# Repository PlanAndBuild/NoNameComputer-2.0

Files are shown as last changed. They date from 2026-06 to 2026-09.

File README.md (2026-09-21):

<div align="center">
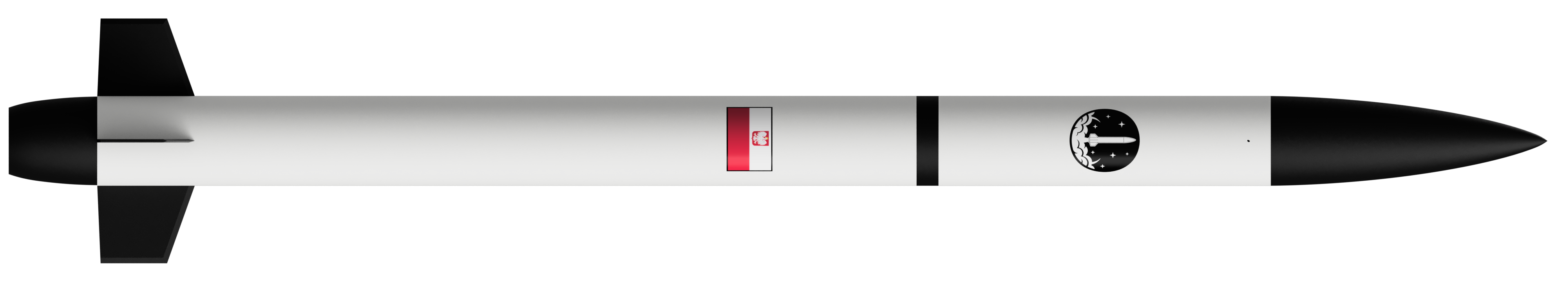
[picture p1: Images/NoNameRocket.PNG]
Render projektu
  
</div>

---

<h1 align="center">NNCpro</h1>

<h3 align="center">AKA NoNameComputer 2.0</h3>

<p align="center">
 <small><I>Built for sky.<I></small>
</p>

<p align="center">
  <b>NNCpro is a fligth computer designed mainly for rockets but it also can be used for other vehicles.</b>
  <br>
  <b>It is designed to collect data from all of the sensor, sending it IRL back down to the earth via radio link, deploy parachutes, steer rocket in flight using aerodynamic control or TVC and at the end send live location. </b>
  </br>
  <em>We have designed it for our rockets because there is no comercial computers or if there is something it's very expensive. We actually like designig electronics and thats why we're even here.</em>
</p>

## Features

**8x Servo outputs** ***(PWM channels)***

**6x Pyrotechniacal channels** ***(used for firing parachute charges, motor ignitions etc.)***

**Long-Range radio** ***(based on two LoRa modules for simultaneous transmiting and reciveing)***

**Current and Voltage sensing** ***(based on INA3221 three channel current sensor)***

**Audio signaling** ***(using passive buzzer with possibility of modulation sound wave)***

**Flash memory for storing software and flight data in flight**

**micro-SD card slot for saving fligth data after landing**

**3,3v and 5v power supply**

**ARGB LEDs for signaling computer states**

---
## Sensors
| Sensor Type | Primary Component |
| :--- | :--- |
| **Barometer main** | `MS5611` (High precision) |
| **Barometer secondary** |`BMP390` (Redundant) |
| **Inertail Mesurment Unit main**| `LSM6DSV80XTR` (6-DoF Main) |
| **Inertail Mesurment Unit secondary** |`LSM6DSO32XTR` (6-DoF Secondary) |
| **High-G Acceleration** | `H3LIS200DLTR` (Up to $\pm200\text{g}$) |
| **Magnetometer** | `MMC5983MA` (3-axis Compass) |
| **GNSS (GPS)** | `u-blox MAX-M10M-20b` |
---
## Images

<table align="center" border="0" cellpadding="0" cellspacing="0">
  <tr>
    <td>
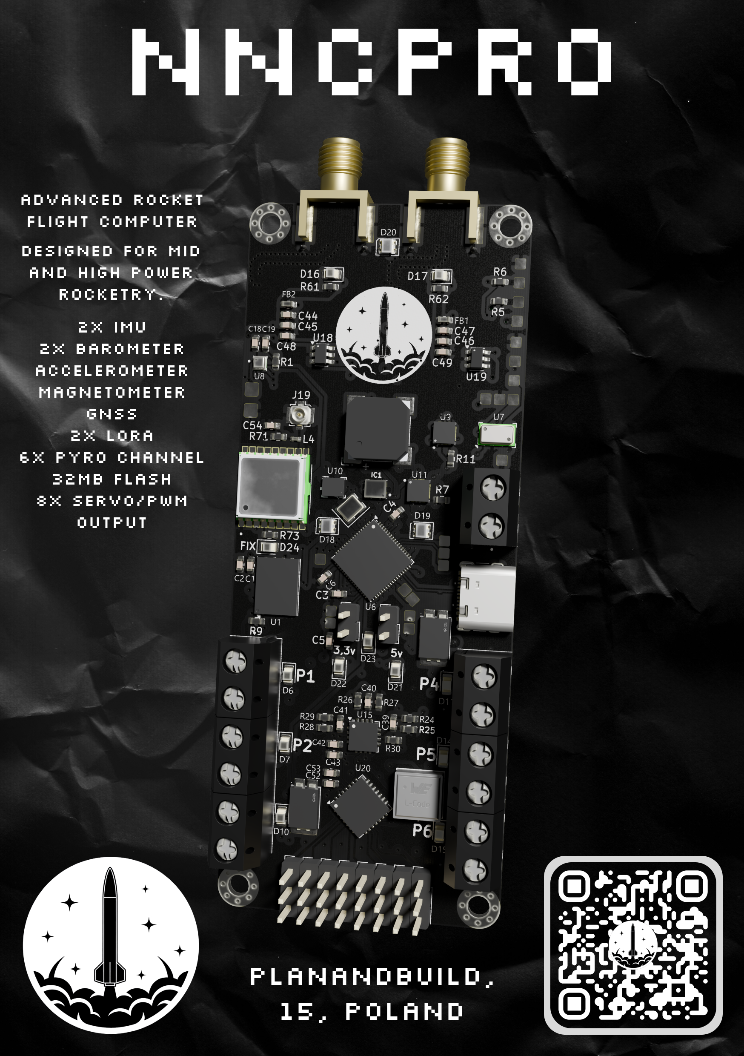
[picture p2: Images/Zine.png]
NNCpro Zine
      
    </td>
    <td>
      NNCpro Render
    </td>
  </tr>
</table>

### schematics:

 <div align="center">
  
  
  
  
  
  
</div>
 
## ⚖️ License

This project is licensed under the **Creative Commons Attribution-NonCommercial-ShareAlike 4.0 International (CC BY-NC-SA 4.0)** License.

[][cc-by-nc-sa]

You are free to share and adapt this material under the following terms:
* **Attribution** — You must give appropriate credit to the original author.
* **NonCommercial** — You may not use the material for commercial purposes.
* **ShareAlike** — If you remix, transform, or build upon the material, you must distribute your contributions under the same license.

## BOM
| Item No. | Qty | Value | Manufacturer Part Number (MPN) | Supplier Part Number | Unit Price | Total Price |
| :---: | :---: | :--- | :--- | :--- | :---: | :---: |
| | **--- CAPACITORS ---** | | | | | |
| 1 | 1 | 10nF | 0603X7R103K250NT | [C49326603](https://www.lcsc.com/product-detail/C49326603.html) | $0.0034 | $0.0034 |
| 2 | 33 | 100nF | FCC0603B104K500CT | [C5137636](https://www.lcsc.com/product-detail/C5137636.html) | $0.0147 | $0.4851 |
| 3 | 5 | 1uF | CL10B105KA8NNNC | [C29936](https://www.lcsc.com/product-detail/C29936.html) | $0.0218 | $0.1090 |
| 4 | 2 | 2.2uF | CL10A225KO8NNNC | [C23630](https://www.lcsc.com/product-detail/C23630.html) | $0.0093 | $0.0186 |
| 5 | 1 | 4.7uF | CL10A475KO8NNNC | [C19666](https://www.lcsc.com/product-detail/C19666.html) | $0.0227 | $0.0227 |
| 6 | 5 | 10uF | CL10A106MA8NRNC | [C96446](https://www.lcsc.com/product-detail/C96446.html) | $0.0532 | $0.2660 |
| 7 | 5 | 22uF | CL10A226MP8NUNE | [C86295](https://www.lcsc.com/product-detail/C86295.html) | $0.0380 | $0.1900 |
| 8 | 4 | 47uF | CL21A476MRYNNNE | [C377776](https://www.lcsc.com/product-detail/C377776.html) | $0.0542 | $0.2168 |
| | **--- RESISTORS ---** | | | | | |
| 9 | 3 | 0.03Ω | YLRY06-1-30F | [C20608713](https://www.lcsc.com/product-detail/C20608713.html) | $0.0390 | $0.1170 |
| 10 | 13 | 10Ω | 1RC0603J0100 | [C54531635](https://www.lcsc.com/product-detail/C54531635.html) | $0.0012 | $0.0156 |
| 11 | 7 | 220Ω | HRC0603F2200ENTN | [C54920883](https://www.lcsc.com/product-detail/C54920883.html) | $0.0011 | $0.0077 |
| 12 | 1 | 560Ω | GR0603J560RT5G00 | [C49653272](https://www.lcsc.com/product-detail/C49653272.html) | $0.0008 | $0.0008 |
| 13 | 1 | 1kΩ | FRC0603F1001TS | [C2907002](https://www.lcsc.com/product-detail/C2907002.html) | $0.0023 | $0.0023 |
| 14 | 2 | 4.7kΩ | HRC0603J472 ENTN | [C54921051](https://www.lcsc.com/product-detail/C54921051.html) | $0.0010 | $0.0020 |
| 15 | 2 | 5.1kΩ | RTT035101FTP | [C103686](https://www.lcsc.com/product-detail/C103686.html) | $0.0012 | $0.0024 |
| 16 | 30 | 10kΩ | FRC0603F1002TS | [C2906982](https://www.lcsc.com/product-detail/C2906982.html) | $0.0023 | $0.0690 |
| 17 | 2 | 15kΩ | SCR0603J15K | [C3017711](https://www.lcsc.com/product-detail/C3017711.html) | $0.0009 | $0.0018 |
| 18 | 1 | 30kΩ | CL0603JN30KP | [C49254202](https://www.lcsc.com/product-detail/C49254202.html) | $0.0011 | $0.0110 |
| 19 | 1 | 42.2kΩ | RS-03K4222FT | [C321903](https://www.lcsc.com/product-detail/C321903.html) | $0.0006 | $0.0006 |
| 20 | 10 | 100kΩ | CL0603JN100KP | [C46635231](https://www.lcsc.com/product-detail/C46635231.html) | $0.0011 | $0.0110 |
| 21 | 1 | 110kΩ | CL0603FN110KP | [C48996812](https://www.lcsc.com/product-detail/C48996812.html) | $0.0012 | $0.0012 |
| 22 | 1 | 135kΩ | RT0603BRD07135KL | [C861113](https://www.lcsc.com/product-detail/C861113.html) | $0.0284 | $0.0284 |
| 23 | 1 | 330kΩ | GR0603J330KT5G00 | [C49656714](https://www.lcsc.com/product-detail/C49656714.html) | $0.0008 | $0.0008 |
| | **--- INDUCTORS / CHOKES ---** | | | | | |
| 24 | 2 | 27nH | LQG15HS27NJ02D | [C12669](https://www.lcsc.com/product-detail/C12669.html) | $0.0282 | $0.0564 |
| 25 | 1 | 680nH | 7443934450068 | [710-7443934450068](https://www.mouser.pl/ProductDetail/Wurth-Elektronik/7443934450068) | $1.8700 | $1.8700 |
| 26 | 1 | 1.5uH | AFE201612S1R5MBT | [C41347749](https://www.lcsc.com/product-detail/C41347749.html) | $0.0389 | $0.0389 |
| | **--- DIODES / TRANSISTORS ---** | | | | | |
| 27 | 6 | ZMM3V0-TD | ZMM3V0-TD | [C46550821](https://www.lcsc.com/product-detail/C46550821.html) | $0.0064 | $0.0384 |
| 28 | 7 | DO2300B | DO2300B | [C41367404](https://www.lcsc.com/product-detail/C41367404.html) | $0.0190 | $0.1330 |
| 29 | 12 | LED RED | GL0805UR01 | [C51933307](https://www.lcsc.com/product-detail/C51933307.html) | $0.0046 | $0.0552 |
| 30 | 1 | SI1016CX-T1-GE3 | SI1016CX-T1-GE3 | [C727293](https://www.lcsc.com/product-detail/C727293.html) | $0.9442 | $0.9442 |
| 31 | 3 | SP15100L | SP15100L | [C20199370](https://www.lcsc.com/product-detail/C20199370.html) | $0.1170 | $0.3510 |
| 32 | 3 | WS2812B-2020 | XL-0807RGBC-2812B-S | [C41413181](https://www.lcsc.com/product-detail/C41413181.html) | $0.0345 | $0.1035 |
| | **--- INTEGRATED CIRCUITS (ICs) ---** | | | | | |
| 33 | 2 | 74LVC2G04LT06ARCQ | 74LVC2G04LT06ARCQ | [C46527078](https://www.lcsc.com/product-detail/C46527078.html) | $0.0404 | $0.0808 |
| 34 | 1 | BMP390L | BMP390L | [828-BMP390TR-ND](https://www.digikey.pl/en/products/detail/bosch-sensortec/BMP390/16164575) | $3.3000 | $3.3000 |
| 35 | 2 | E220-400M22S | E220-400M22S | [C2971737](https://www.lcsc.com/product-detail/C2971737.html) | $2.7215 | $5.4430 |
| 36 | 1 | H3LIS200DLTR | H3LIS200DLTR | [497-15698-2-ND](https://www.digikey.pl/en/products/detail/stmicroelectronics/H3LIS200DLTR/5268010) | $8.4000 | $8.4000 |
| 37 | 1 | INA3221 | INA3221AIRGVR | [C181255](https://www.lcsc.com/product-detail/C181255.html) | $1.4247 | $1.4247 |
| 38 | 1 | LSM6DSO32 | LSM6DSO32 | [497-LSM6DSO32XTR-ND](https://www.digikey.pl/en/products/detail/stmicroelectronics/LSM6DSO32XTR/14291421) | $4.8900 | $4.8900 |
| 39 | 1 | LSM6DSV80XTR | LSM6DSV80XTR | [497-LSM6DSV80XTR-ND](https://www.digikey.pl/en/products/detail/stmicroelectronics/LSM6DSV80XTR/26371340) | $6.5100 | $6.5100 |
| 40 | 1 | LT6000CDCB#TRMPBF | LT6000CDCB#TRMPBF | [C672644](https://www.lcsc.com/product-detail/C672644.html) | $3.3445 | $3.3445 |
| 41 | 1 | MAX-M10M-20B | MAX-M10M-20B | [672-MAX-M10M-20BTR-ND](https://www.digikey.pl/en/products/detail/u-blox/MAX-M10M-20B/28314774) | $7.5600 | $7.5600 |
| 42 | 1 | MMC5983MA | MMC5983MA | [C404329](https://www.lcsc.com/product-detail/C404329.html) | $2.2672 | $2.2672 |
| 43 | 1 | MS5611 | MS5611-01BA | [C15639](https://www.lcsc.com/product-detail/C15639.html) | $7.1145 | $7.1145 |
| 44 | 1 | NC7WZ07P6X | NC7WZ07P6X | [C95342](https://www.lcsc.com/product-detail/C95342.html) | $0.0564 | $0.0564 |
| 45 | 1 | PCA9685BS | PCA9685BS | [C5191634](https://www.lcsc.com/product-detail/C5191634.html) | $4.4014 | $4.4014 |
| 46 | 1 | STM32H562RIVx | STM32H562RIV6 | [497-STM32H562RIV6-ND](https://www.digikey.pl/en/products/detail/stmicroelectronics/STM32H562RIV6/21348982) | $7.3400 | $7.3400 |
| 47 | 1 | TPS564242DRLR | TPS564242DRLR | [296-TPS564242DRLRTR-ND](https://www.digikey.pl/en/products/detail/texas-instruments/TPS564242DRLR/16585669) | $0.5800 | $0.5800 |
| 48 | 1 | TPS56C230RJER | TPS56C230RJER | [C1849534](https://www.lcsc.com/product-detail/C1849534.html) | $0.5300 | $0.5300 |
| 49 | 1 | W25Q512JVE | W25Q512JVEIQ | [C2986165](https://www.lcsc.com/product-detail/C2986165.html) | $6.7941 | $6.7941 |
| | **--- CONNECTORS ---** | | | | | |
| 50 | 2 | Conn_01x02_Pin | 2.54mm Header 2pin | [Numer](Link) | | |
| 51 | 8 | Conn_01x03_Pin | 2.54mm Header 3pin | [Numer](Link) | | |
| 52 | 2 | SMA_Connector | HL-SMA-KHDC5T | [C19712117](https://www.lcsc.com/product-detail/C19712117.html) | $2.9083 | $5.8166 |
| 53 | 1 | U.fl_Connetor | 5001-RF00001-03R1-00 | [C48689029](https://www.lcsc.com/product-detail/C48689029.html) | $0.0338 | $0.0338 |
| 54 | 1 | MLD-TF PUSH-H18 | MLD-TF PUSH-H18 | [C52750848](https://www.lcsc.com/product-detail/C52750848.html) | $0.0421 | $0.0421 |
| 55 | 7 | Screw_Terminal_01x02 | KF301-2P | [C474881](https://www.lcsc.com/product-detail/C474881.html) | $0.1008 | $0.7056 |
| 56 | 1 | USB_C_Receptacle_USB2.0_16P | F32258MUBCE2O | [C5917305](https://www.lcsc.com/product-detail/C5917305.html) | $0.3052 | $0.3052 |
| | **--- MISCELLANEOUS ---** | | | | | |
| 57 | 6 | 500mA | CF06V5TR50 | [C163116](https://www.lcsc.com/product-detail/C163116.html) | $0.0386 | $0.2316 |
| 58 | 3 | 600ohm | CBG160808U601T | [C73326](https://www.lcsc.com/product-detail/C73326.html) | $0.0113 | $0.0678 |
| 59 | 1 | Buzzer | YX-SMD8530P | [C781886](https://www.lcsc.com/product-detail/C781886.html) | $0.3755 | $0.3755 |
| 60 | 1 | Crystal_GND24 | F32258MUBCE2O | [C5917305](https://www.lcsc.com/product-detail/C5917305.html) | $0.3052 | $0.3052 |
| | **--- ADDITIONAL ELEMENTS ---** | | | | | |
| 61 | 4 | Screws | Any M3 screw |  |  |  |
| 62 | 1 | PCB Board | 4layer PCB | - | $7.0000 | $7.0000 |
| | | | | | | |
| **SUMMARY** | | | | | | **Total: $90.28** |

[cc-by-nc-sa]: http://creativecommons.org/licenses/by-nc-sa/4.0/
[cc-by-nc-sa-shield]: https://img.shields.io/badge/License-CC%20BY--NC--SA%204.0-lightgrey.svg

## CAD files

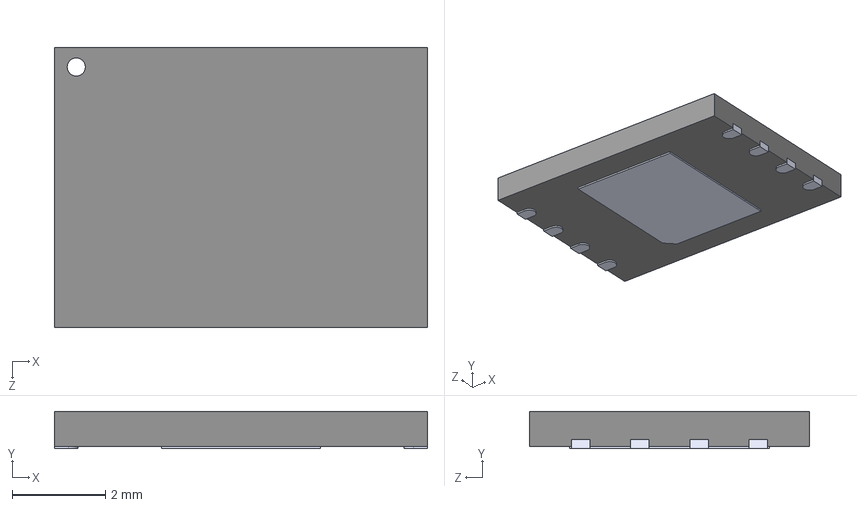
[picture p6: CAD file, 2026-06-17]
Board/3DModels/W25Q256JVEIQ TR--3DModel-STEP-269445.STEP
8.00 x 0.8 x 6.00 mm

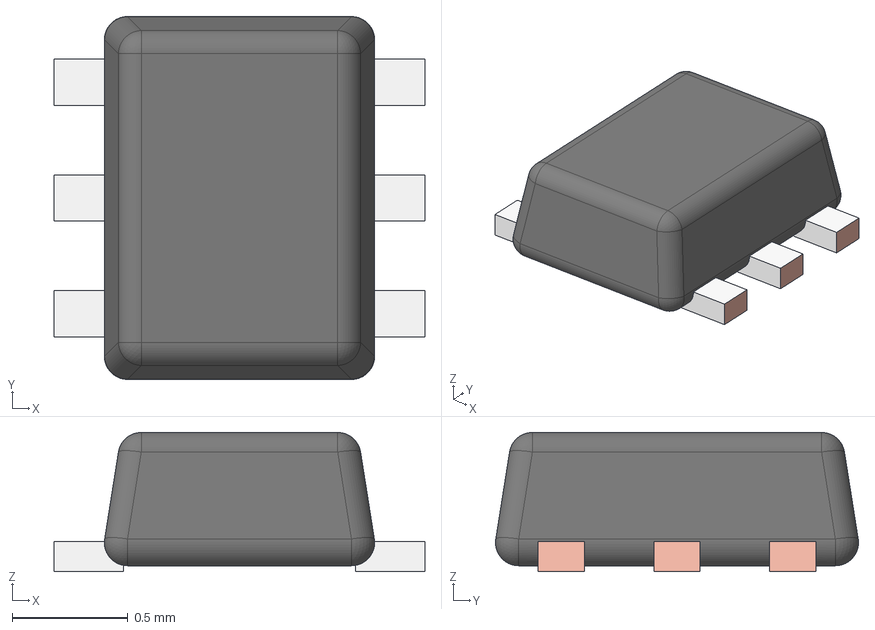
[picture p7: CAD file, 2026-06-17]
Board/3DModels/DRL0006A.stp
1.60 x 1.57 x 0.6 mm
FRAME-DRL0006A
BODY-SOT
PIN1-ID

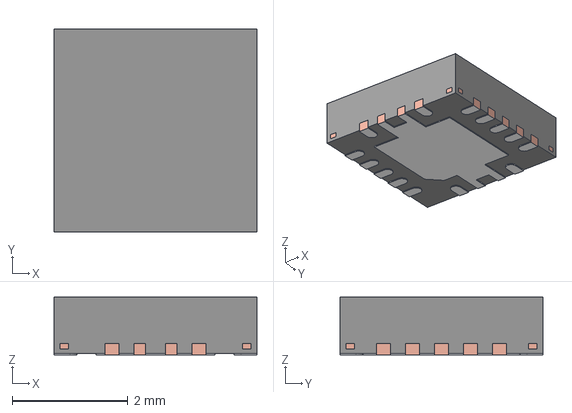
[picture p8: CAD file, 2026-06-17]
Board/3DModels/RHL0014A.stp
3.50 x 3.50 x 1.00 mm
FRAME

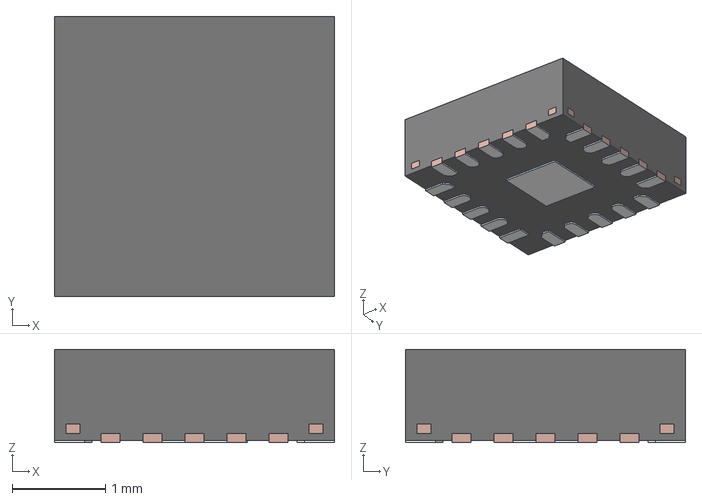
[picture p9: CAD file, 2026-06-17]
Board/3DModels/TPS56C230RJER.stp
3.00 x 3.00 x 1.00 mm
FRAME

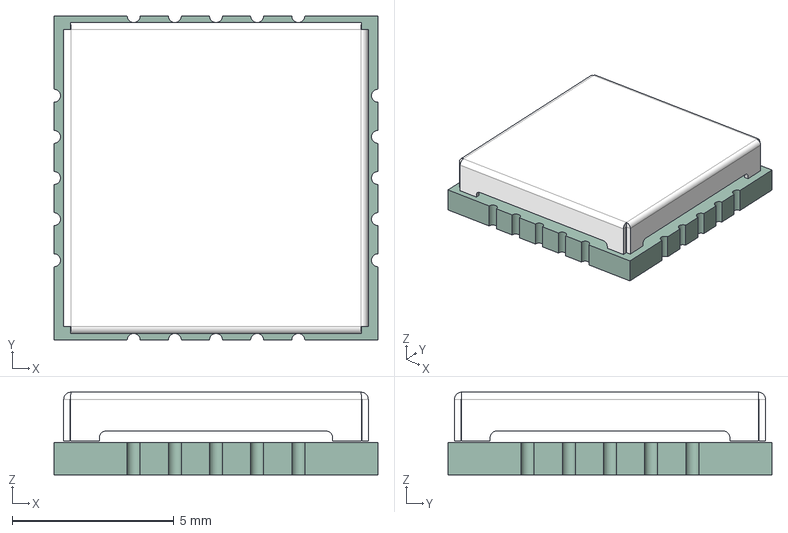
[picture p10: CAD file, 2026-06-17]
Board/3DModels/E220-400MM22S.step
10.0 x 10.0 x 2.55 mm
PBZ-135
10705-V1.1_PCB

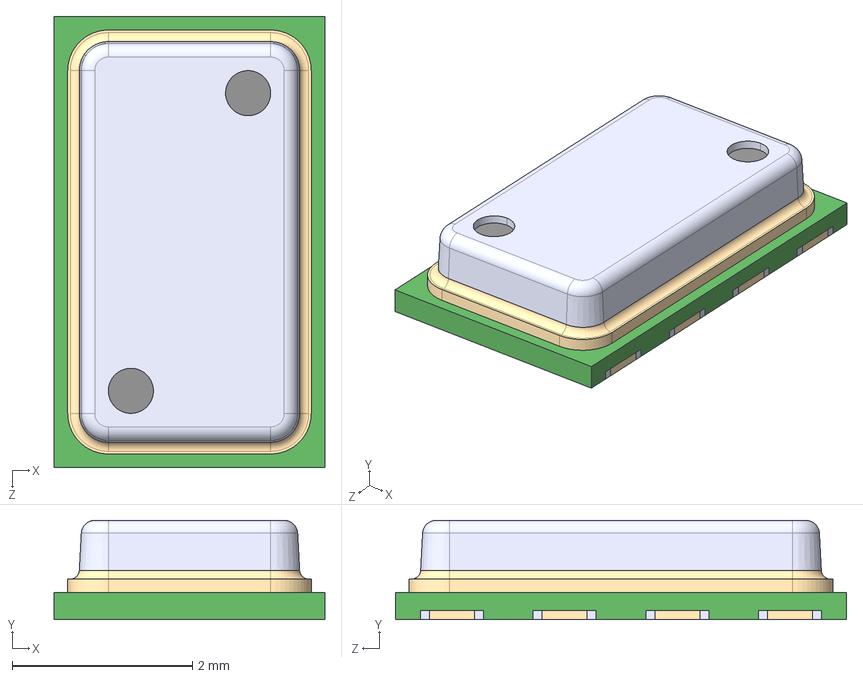
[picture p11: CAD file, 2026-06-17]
Board/3DModels/MS5611-01BA03--3DModel-STEP-510211.STEP
3.00 x 1.10 x 5.00 mm

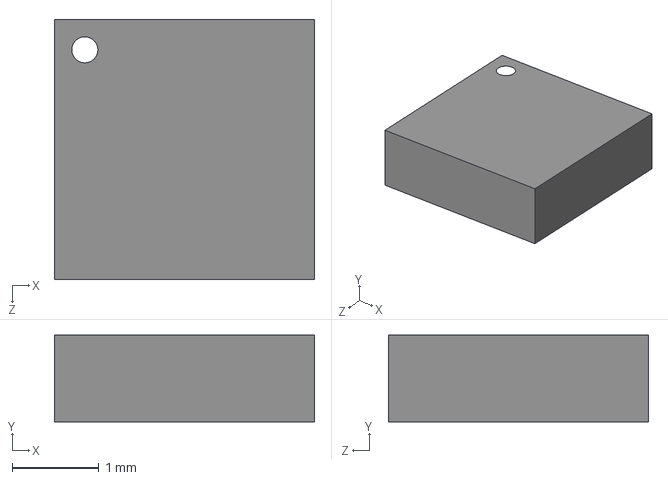
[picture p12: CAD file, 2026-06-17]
Board/3DModels/MMC5983MA.step
3.00 x 1.00 x 3.00 mm

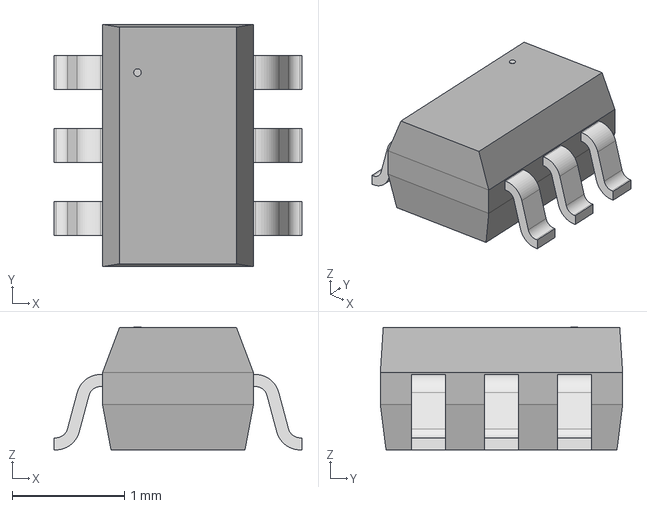
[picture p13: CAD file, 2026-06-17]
Board/3DModels/SC-70-6_PSM.step
2.21 x 2.16 x 1.09 mm

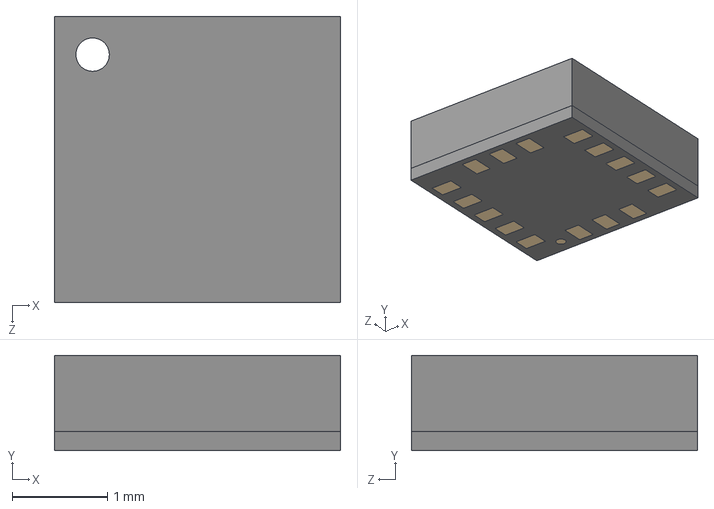
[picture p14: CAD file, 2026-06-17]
Board/3DModels/H3LIS200DLTR.step
3.00 x 1.00 x 3.00 mm

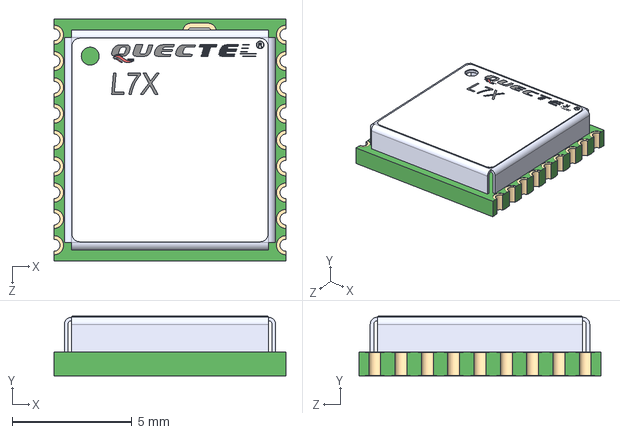
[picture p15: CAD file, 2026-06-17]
Board/3DModels/L76-L.step
9.70 x 2.49 x 10.1 mm

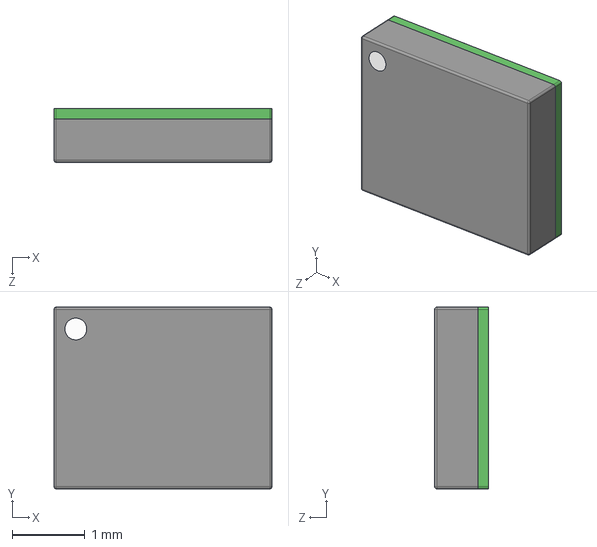
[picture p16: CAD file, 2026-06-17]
Board/3DModels/LSM6DSV80XTR.stp
3.00 x 2.50 x 0.74 mm

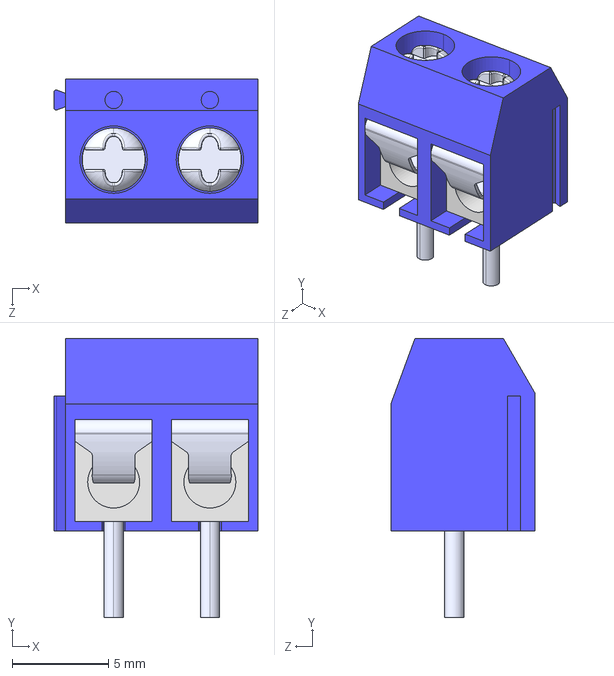
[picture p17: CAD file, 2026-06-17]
Board/3DModels/KF301-2P.step
10.6 x 14.5 x 7.50 mm

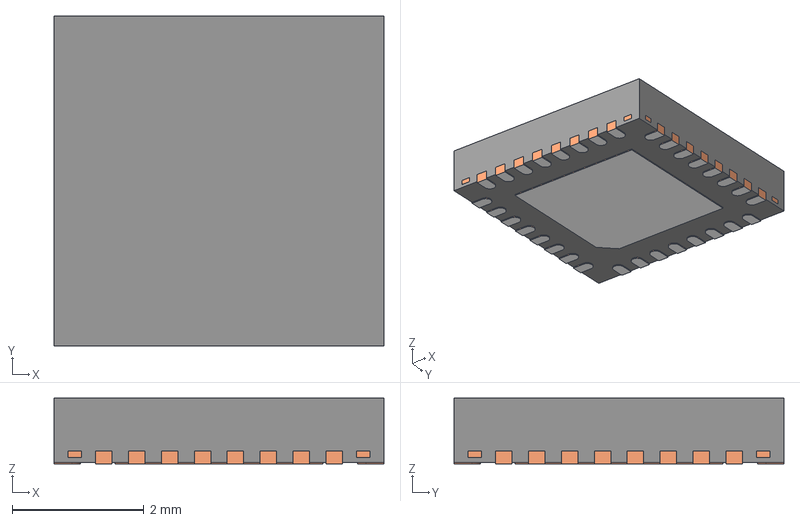
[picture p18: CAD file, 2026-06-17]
Board/3DModels/TLC5940RHBR.stp
5.00 x 5.00 x 1.00 mm
BODY-QFN
FRAME-RHB0032D
PIN1-ID

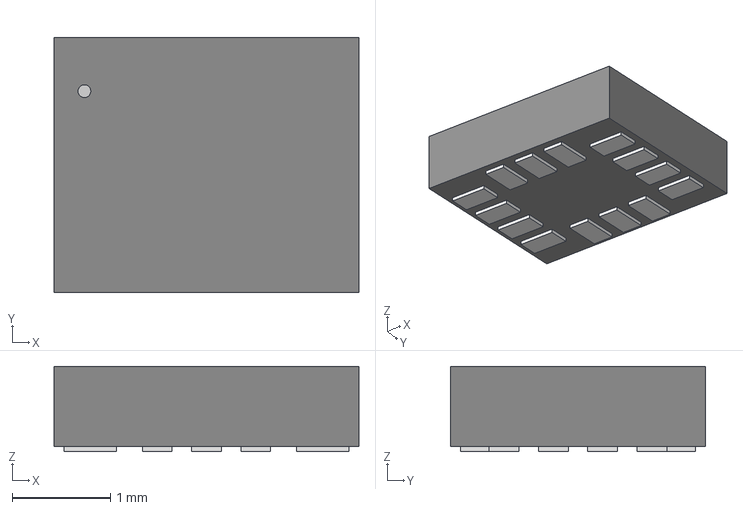
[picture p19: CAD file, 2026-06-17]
Board/3DModels/LGA-14L_2P5X3X0P83_STM.step
3.10 x 2.59 x 0.866 mm

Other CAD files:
Board/3DModels/W25Q256JVEIQ_TR.step
Board/3DModels/BMP390L.step
Board/3DModels/WS2812B2020--3DModel-STEP-269445.STEP

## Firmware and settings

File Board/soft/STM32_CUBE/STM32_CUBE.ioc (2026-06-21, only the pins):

Mcu.UserName=STM32H562RIVx
PA0.Signal=UART4_TX
PA1.GPIO_Label=GPS_RST
PA1.Signal=GPIO_Output
PA10.GPIO_Label=CS_MAG
PA10.Signal=GPIO_Output
PA11.Signal=USB_DM
PA12.Signal=USB_DP
PA13(JTMS/SWDIO).GPIO_Label=CS_H3L
PA13(JTMS/SWDIO).Signal=GPIO_Output
PA14(JTCK/SWCLK).GPIO_Label=CS_LSM1
PA14(JTCK/SWCLK).Signal=GPIO_Output
PA15(JTDI).GPIO_Label=BUSY_2
PA15(JTDI).Signal=GPIO_Input
PA3.Signal=OCTOSPI1_CLK
PA4.GPIO_Label=EN_5V
PA4.Signal=GPIO_Output
PA5.GPIO_Label=LED_1
PA5.Signal=GPIO_Output
PA6.Signal=OCTOSPI1_IO3
PA7.GPIO_Label=PYRO_1
PA7.Signal=GPIO_Output
PA9.GPIO_Label=CS_MS5611
PA9.Signal=GPIO_Output
PB0.Signal=OCTOSPI1_IO1
PB1.GPIO_Label=P_DET_2
PB1.Signal=GPIO_Input
PB10.Signal=I2C2_SCL
PB11.Signal=I2C2_SDA
PB12.GPIO_Label=P_DET_3
PB12.Signal=GPIO_Input
PB13.GPIO_Label=P_DET_6
PB13.Signal=GPIO_Input
PB14.GPIO_Label=PYRO_6
PB14.Signal=GPIO_Output
PB15.GPIO_Label=P_DET_5
PB15.Signal=GPIO_Input
PB2.GPIO_Label=PYRO_3
PB2.Signal=GPIO_Output
PB6.Signal=OCTOSPI1_NCS
PB7.GPIO_Label=CS_LoRa2
PB7.Signal=GPIO_Output
PB8.Signal=UART4_RX
PB9.GPIO_Label=DIO1_2
PB9.Signal=GPIO_Output
PC0.GPIO_Label=SepDet1
PC0.Signal=GPIO_Input
PC1.GPIO_Label=SepDet2
PC1.Signal=GPIO_Input
PC10.Signal=SPI3_SCK
PC11.Signal=SPI3_MISO
PC12.Signal=SPI3_MOSI
PC13.GPIO_Label=CS_LoRa1
PC13.Signal=GPIO_Output
PC14-OSC32_IN(OSC32_IN).GPIO_Label=DIO1_1
PC14-OSC32_IN(OSC32_IN).Signal=GPIO_Output
PC15-OSC32_OUT(OSC32_OUT).GPIO_Label=CS_BMP390
PC15-OSC32_OUT(OSC32_OUT).Signal=GPIO_Output
PC2.Signal=OCTOSPI1_IO2
PC3.Signal=OCTOSPI1_IO0
PC4.GPIO_Label=P_DET_1
PC4.Signal=GPIO_Input
PC5.GPIO_Label=PYRO_2
PC5.Signal=GPIO_Output
PC6.GPIO_Label=PYRO_4
PC6.Signal=GPIO_Output
PC7.GPIO_Label=CS_SD
PC7.Signal=GPIO_Output
PC8.GPIO_Label=CS_LSM2
PC8.Signal=GPIO_Output
PD11.GPIO_Label=PYRO_5
PD11.Signal=GPIO_Output
PD12.GPIO_Label=P_DET_4
PD12.Signal=GPIO_Input
PE0.GPIO_Label=BUSY_1
PE0.Signal=GPIO_Input
PH0-OSC_IN(PH0).Signal=RCC_OSC_IN
PH1-OSC_OUT(PH1).Signal=RCC_OSC_OUT

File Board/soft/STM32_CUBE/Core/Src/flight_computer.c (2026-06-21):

#include "flight_computer.h"
#include "sensor_ms5611.h"
#include "sensor_bmp390.h"
#include "sensor_lsm6dsv.h"
#include "sensor_lsm6dso.h"
#include "sensor_h3lis200.h"
#include "sensor_mmc5983.h"
#include "sensor_ina3221.h"
#include "gps_parser.h"
#include "lora_llcc68.h"
#include "flash_w25q.h"
#include "sd_card.h"
#include "pca9685.h"
#include "spi_common.h"
#include <stdio.h>
#include <string.h>

// Shared handles and states
extern UART_HandleTypeDef huart4;

static FlightState_t current_state = STATE_IDLE;
static float ground_altitude = 0.0f;
static uint32_t flight_start_time = 0;
static uint32_t flash_write_address = 0;
static uint32_t log_count = 0;

// Device handles
static MS5611_t ms5611;
static BMP390_t bmp390;
static LSM6DSV_t imu_main;
static LSM6DSO_t imu_sub;
static H3LIS200_t high_g;
static MMC5983_t mag;
static INA3221_t power_mon;
static GPS_Data_t *gps_ptr;

static LoRa_t lora_tx;
static LoRa_t lora_rx;

// 2-State Kalman Filter state: x = [alt, vel]^T
static float x_alt = 0.0f;
static float x_vel = 0.0f;
static float P_00 = 10.0f;
static float P_01 = 0.0f;
static float P_10 = 0.0f;
static float P_11 = 10.0f;

// Filter variances (tuning parameters)
static const float Q_alt = 0.1f;
static const float Q_vel = 0.5f;
static const float R_baro = 1.2f;

static void Kalman_Predict(float accel, float dt)
{
  // State extrapolation: x_k = F * x_{k-1} + B * u
  x_alt = x_alt + x_vel * dt + 0.5f * accel * dt * dt;
  x_vel = x_vel + accel * dt;

  // Covariance extrapolation: P = F * P * F^T + Q
  float P00_new = P_00 + dt * (P_10 + P_01 + dt * P_11) + Q_alt;
  float P01_new = P_01 + dt * P_11 + Q_alt;
  float P10_new = P_10 + dt * P_11 + Q_alt;
  float P11_new = P_11 + Q_vel;

  P_00 = P00_new;
  P_01 = P01_new;
  P_10 = P10_new;
  P_11 = P11_new;
}

static void Kalman_Update(float meas_alt)
{
  // Kalman Gain: K = P * H^T * (H * P * H^T + R)^-1
  float S = P_00 + R_baro;
  float K_0 = P_00 / S;
  float K_1 = P_10 / S;

  // State update: x = x + K * (z - H * x)
  float err = meas_alt - x_alt;
  x_alt = x_alt + K_0 * err;
  x_vel = x_vel + K_1 * err;

  // Covariance update: P = (I - K * H) * P
  float P_00_new = (1.0f - K_0) * P_00;
  float P_01_new = (1.0f - K_0) * P_01;
  float P_10_new = -K_1 * P_00 + P_10;
  float P_11_new = -K_1 * P_01 + P_11;

  P_00 = P_00_new;
  P_01 = P_01_new;
  P_10 = P_10_new;
  P_11 = P_11_new;
}

// Continuity checking helper
static uint8_t CheckPyroContinuity(uint8_t channel)
{
  GPIO_PinState state = GPIO_PIN_RESET;
  switch (channel)
  {
    case 1: state = HAL_GPIO_ReadPin(P_DET_1_GPIO_Port, P_DET_1_Pin); break;
    case 2: state = HAL_GPIO_ReadPin(P_DET_2_GPIO_Port, P_DET_2_Pin); break;
    case 3: state = HAL_GPIO_ReadPin(P_DET_3_GPIO_Port, P_DET_3_Pin); break;
    case 4: state = HAL_GPIO_ReadPin(P_DET_4_GPIO_Port, P_DET_4_Pin); break;
    case 5: state = HAL_GPIO_ReadPin(P_DET_5_GPIO_Port, P_DET_5_Pin); break;
    case 6: state = HAL_GPIO_ReadPin(P_DET_6_GPIO_Port, P_DET_6_Pin); break;
    default: break;
  }
  // Low logic level usually indicates igniter is connected (closing shunt to GND), 
  // High level means open circuit. Depending on schematic, let's return 1 for connected, 0 for open.
  return (state == GPIO_PIN_RESET) ? 1 : 0;
}

static void FirePyro(uint8_t channel)
{
  switch (channel)
  {
    case 1:
      HAL_GPIO_WritePin(PYRO_1_GPIO_Port, PYRO_1_Pin, GPIO_PIN_SET);
      HAL_Delay(1000); // 1-second pulse
      HAL_GPIO_WritePin(PYRO_1_GPIO_Port, PYRO_1_Pin, GPIO_PIN_RESET);
      break;
    case 2:
      HAL_GPIO_WritePin(PYRO_2_GPIO_Port, PYRO_2_Pin, GPIO_PIN_SET);
      HAL_Delay(1000);
      HAL_GPIO_WritePin(PYRO_2_GPIO_Port, PYRO_2_Pin, GPIO_PIN_RESET);
      break;
    case 3:
      HAL_GPIO_WritePin(PYRO_3_GPIO_Port, PYRO_3_Pin, GPIO_PIN_SET);
      HAL_Delay(1000);
      HAL_GPIO_WritePin(PYRO_3_GPIO_Port, PYRO_3_Pin, GPIO_PIN_RESET);
      break;
    case 4:
      HAL_GPIO_WritePin(PYRO_4_GPIO_Port, PYRO_4_Pin, GPIO_PIN_SET);
      HAL_Delay(1000);
      HAL_GPIO_WritePin(PYRO_4_GPIO_Port, PYRO_4_Pin, GPIO_PIN_RESET);
      break;
    case 5:
      HAL_GPIO_WritePin(PYRO_5_GPIO_Port, PYRO_5_Pin, GPIO_PIN_SET);
      HAL_Delay(1000);
      HAL_GPIO_WritePin(PYRO_5_GPIO_Port, PYRO_5_Pin, GPIO_PIN_RESET);
      break;
    case 6:
      HAL_GPIO_WritePin(PYRO_6_GPIO_Port, PYRO_6_Pin, GPIO_PIN_SET);
      HAL_Delay(1000);
      HAL_GPIO_WritePin(PYRO_6_GPIO_Port, PYRO_6_Pin, GPIO_PIN_RESET);
      break;
    default:
      break;
  }
}

// Dump records from W25Q128 Flash to SD card in CSV format
static void DumpLogsToSDCard(void)
{
  uint8_t block_buf[512];
  uint32_t flash_address = 0;
  FlightLog_t log_record;
  uint32_t csv_sector_idx = 0;
  uint32_t current_block_offset = 0;

  // Let's create an SD card file pre-allocated size of 15000 sectors (approx 7.5MB)
  if (FAT32_FormatAndCreateFile(15000) != HAL_OK)
  {
    return; // SD format failed
  }

  // Pre-fill block buffer with CSV header
  memset(block_buf, 0, 512);
  int header_len = sprintf((char*)block_buf, 
    "Time(ms),State,KalmanAlt(m),KalmanVel(m/s),MS5611Alt(m),BMP390Alt(m),AccX(g),AccY(g),AccZ(g),IMUAX(g),IMUAY(g),IMUAZ(g),IMUGX(deg/s),IMUGY,IMUGZ,MagX(G),MagY,MagZ,V_Batt(V),I_Sys(A),Lat,Lon,GpsAlt\n");
  
  current_block_offset = header_len;

  for (uint32_t i = 0; i < log_count; i++)
  {
    // Read record from Flash
    if (W25Q_Read(flash_address, (uint8_t*)&log_record, sizeof(FlightLog_t)) != HAL_OK) break;
    flash_address += sizeof(FlightLog_t);

    // Format CSV row
    char row_buf[300];
    int row_len = sprintf(row_buf, 
      "%lu,%d,%.2f,%.2f,%.2f,%.2f,%.3f,%.3f,%.3f,%.3f,%.3f,%.3f,%.2f,%.2f,%.2f,%.3f,%.3f,%.3f,%.2f,%.3f,%.6f,%.6f,%.1f\n",
      log_record.timestamp_ms, log_record.state, log_record.kalman_alt, log_record.kalman_vel,
      log_record.ms5611_alt, log_record.bmp390_alt, log_record.ax, log_record.ay, log_record.az,
      log_record.imu_ax, log_record.imu_ay, log_record.imu_az, log_record.imu_gx, log_record.imu_gy, log_record.imu_gz,
      log_record.mx, log_record.my, log_record.mz, log_record.battery_v, log_record.system_current,
      log_record.gps_lat, log_record.gps_lon, log_record.gps_alt);

    if (current_block_offset + row_len >= 512)
    {
      // Write full sector buffer to SD
      FAT32_WriteFileSectors(csv_sector_idx++, block_buf, 1);
      
      // Setup next buffer
      memset(block_buf, 0, 512);
      memcpy(block_buf, row_buf, row_len);
      current_block_offset = row_len;
    }
    else
    {
      memcpy(block_buf + current_block_offset, row_buf, row_len);
      current_block_offset += row_len;
    }
  }

  // Write remaining sector buffer
  if (current_block_offset > 0)
  {
    FAT32_WriteFileSectors(csv_sector_idx++, block_buf, 1);
  }
}
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

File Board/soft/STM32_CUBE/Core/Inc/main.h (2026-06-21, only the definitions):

#define CS_LoRa1_Pin GPIO_PIN_13
#define CS_LoRa1_GPIO_Port GPIOC
#define DIO1_1_Pin GPIO_PIN_14
#define DIO1_1_GPIO_Port GPIOC
#define CS_BMP390_Pin GPIO_PIN_15
#define CS_BMP390_GPIO_Port GPIOC
#define SepDet1_Pin GPIO_PIN_0
#define SepDet1_GPIO_Port GPIOC
#define SepDet2_Pin GPIO_PIN_1
#define SepDet2_GPIO_Port GPIOC
#define GPS_RST_Pin GPIO_PIN_1
#define GPS_RST_GPIO_Port GPIOA
#define EN_5V_Pin GPIO_PIN_4
#define EN_5V_GPIO_Port GPIOA
#define LED_1_Pin GPIO_PIN_5
#define LED_1_GPIO_Port GPIOA
#define PYRO_1_Pin GPIO_PIN_7
#define PYRO_1_GPIO_Port GPIOA
#define P_DET_1_Pin GPIO_PIN_4
#define P_DET_1_GPIO_Port GPIOC
#define PYRO_2_Pin GPIO_PIN_5
#define PYRO_2_GPIO_Port GPIOC
#define P_DET_2_Pin GPIO_PIN_1
#define P_DET_2_GPIO_Port GPIOB
#define PYRO_3_Pin GPIO_PIN_2
#define PYRO_3_GPIO_Port GPIOB
#define P_DET_3_Pin GPIO_PIN_12
#define P_DET_3_GPIO_Port GPIOB
#define P_DET_6_Pin GPIO_PIN_13
#define P_DET_6_GPIO_Port GPIOB
#define PYRO_6_Pin GPIO_PIN_14
#define PYRO_6_GPIO_Port GPIOB
#define P_DET_5_Pin GPIO_PIN_15
#define P_DET_5_GPIO_Port GPIOB
#define PYRO_5_Pin GPIO_PIN_11
#define PYRO_5_GPIO_Port GPIOD
#define P_DET_4_Pin GPIO_PIN_12
#define P_DET_4_GPIO_Port GPIOD
#define PYRO_4_Pin GPIO_PIN_6
#define PYRO_4_GPIO_Port GPIOC
#define CS_SD_Pin GPIO_PIN_7
#define CS_SD_GPIO_Port GPIOC
#define CS_LSM2_Pin GPIO_PIN_8
#define CS_LSM2_GPIO_Port GPIOC
#define CS_MS5611_Pin GPIO_PIN_9
#define CS_MS5611_GPIO_Port GPIOA
#define CS_MAG_Pin GPIO_PIN_10
#define CS_MAG_GPIO_Port GPIOA
#define CS_H3L_Pin GPIO_PIN_13
#define CS_H3L_GPIO_Port GPIOA
#define CS_LSM1_Pin GPIO_PIN_14
#define CS_LSM1_GPIO_Port GPIOA
#define BUSY_2_Pin GPIO_PIN_15
#define BUSY_2_GPIO_Port GPIOA
#define CS_LoRa2_Pin GPIO_PIN_7
#define CS_LoRa2_GPIO_Port GPIOB
#define DIO1_2_Pin GPIO_PIN_9
#define DIO1_2_GPIO_Port GPIOB
#define BUSY_1_Pin GPIO_PIN_0
#define BUSY_1_GPIO_Port GPIOE

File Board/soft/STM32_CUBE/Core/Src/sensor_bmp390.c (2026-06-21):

#include "sensor_bmp390.h"
#include "spi_common.h"
#include <math.h>

// BMP390 Registers
#define BMP390_REG_CHIP_ID      0x00
#define BMP390_REG_ERR_REG      0x02
#define BMP390_REG_STATUS       0x03
#define BMP390_REG_DATA_0       0x04 // Pressure data XLSB
#define BMP390_REG_DATA_1       0x05 // Pressure data LSB
#define BMP390_REG_DATA_2       0x06 // Pressure data MSB
#define BMP390_REG_DATA_3       0x07 // Temperature data XLSB
#define BMP390_REG_DATA_4       0x08 // Temperature data LSB
#define BMP390_REG_DATA_5       0x09 // Temperature data MSB
#define BMP390_REG_INT_STATUS   0x11
#define BMP390_REG_OSR          0x1C
#define BMP390_REG_ODR          0x1D
#define BMP390_REG_CONFIG       0x1F
#define BMP390_REG_PWR_CTRL     0x1B
#define BMP390_REG_CMD          0x7E
#define BMP390_REG_CALIB_FIRST  0x31

#define BMP390_CHIP_ID_VAL      0x60
#define BMP390_CMD_SOFTRESET    0xB6

// BMP390 SPI read requires 1 dummy byte after transmitting the register address.
static HAL_StatusTypeDef BMP390_SPI_Read(uint8_t reg, uint8_t *buffer, uint16_t len)
{
  HAL_StatusTypeDef status;
  uint8_t tx_byte = reg | 0x80;
  uint8_t dummy = 0;

  SPI_CS_Select(CS_BMP390_GPIO_Port, CS_BMP390_Pin);
  status = SPI_Transmit(&tx_byte, 1, 50);
  if (status == HAL_OK)
  {
    // Transmit dummy byte as required by BMP390 SPI interface
    status = SPI_Transmit(&dummy, 1, 50);
    if (status == HAL_OK)
    {
      status = SPI_Receive(buffer, len, 100);
    }
  }
  SPI_CS_Deselect(CS_BMP390_GPIO_Port, CS_BMP390_Pin);
  
  return status;
}

static HAL_StatusTypeDef BMP390_SPI_Write(uint8_t reg, uint8_t val)
{
  return SPI_WriteRegister(CS_BMP390_GPIO_Port, CS_BMP390_Pin, reg, val);
}

static void BMP390_ReadCalibration(BMP390_t *dev)
{
  uint8_t calib_buf[21] = {0};
  
  // Read 21 bytes of calibration data starting at register 0x31
  BMP390_SPI_Read(BMP390_REG_CALIB_FIRST, calib_buf, 21);

  dev->calib.T1 = (uint16_t)((calib_buf[1] << 8) | calib_buf[0]);
  dev->calib.T2 = (uint16_t)((calib_buf[3] << 8) | calib_buf[2]);
  dev->calib.T3 = (int8_t)calib_buf[4];
  dev->calib.P1 = (int16_t)((calib_buf[6] << 8) | calib_buf[5]);
  dev->calib.P2 = (int16_t)((calib_buf[8] << 8) | calib_buf[7]);
  dev->calib.P3 = (int8_t)calib_buf[9];
  dev->calib.P4 = (int8_t)calib_buf[10];
  dev->calib.P5 = (uint16_t)((calib_buf[12] << 8) | calib_buf[11]);
  dev->calib.P6 = (uint16_t)((calib_buf[14] << 8) | calib_buf[13]);
  dev->calib.P7 = (int8_t)calib_buf[15];
  dev->calib.P8 = (int8_t)calib_buf[16];
  dev->calib.P9 = (int16_t)((calib_buf[18] << 8) | calib_buf[17]);
  dev->calib.P10 = (int8_t)calib_buf[19];
  dev->calib.P11 = (int8_t)calib_buf[20];
}

HAL_StatusTypeDef BMP390_Init(BMP390_t *dev)
{
  uint8_t chip_id = 0;
  
  // 1. Check chip ID
  BMP390_SPI_Read(BMP390_REG_CHIP_ID, &chip_id, 1);
  if (chip_id != BMP390_CHIP_ID_VAL)
  {
    return HAL_ERROR;
  }

  // 2. Perform soft reset
  BMP390_SPI_Write(BMP390_REG_CMD, BMP390_CMD_SOFTRESET);
  HAL_Delay(10);

  // 3. Read calibration trim parameters
  BMP390_ReadCalibration(dev);

  // 4. Configure Oversampling (ultra high resolution: Press x8, Temp x1)
  BMP390_SPI_Write(BMP390_REG_OSR, 0x03); // osr_p = x8, osr_t = x1

  // 5. Configure ODR (Output Data Rate = 50 Hz)
  BMP390_SPI_Write(BMP390_REG_ODR, 0x02); // 50 Hz

  // 6. Configure IIR Filter (coefficient = 3)
  BMP390_SPI_Write(BMP390_REG_CONFIG, 0x02 << 1);

  // 7. Enable Temp & Press in Normal Mode
  BMP390_SPI_Write(BMP390_REG_PWR_CTRL, 0x33); // press_en=1, temp_en=1, mode=normal (0x33)
  HAL_Delay(20);

  return HAL_OK;
}

// Compensation formulas provided in BMP390 Datasheet section 8.5
static float BMP390_Compensate_Temp(BMP390_t *dev, uint32_t uncomp_temp)
{
  float partial_data1 = (float)(uncomp_temp - dev->calib.T1);
  float partial_data2 = (float)(partial_data1 * dev->calib.T2);
  
  // Store compensated temperature value for pressure compensation
  float comp_temp = partial_data2 + (partial_data1 * partial_data1) * dev->calib.T3;
  return comp_temp;
}

static float BMP390_Compensate_Press(BMP390_t *dev, uint32_t uncomp_press, float comp_temp)
{
  float partial_data1;
  float partial_data2;
  float partial_data3;
  float partial_data4;
  float out1;
  float out2;

  partial_data1 = dev->calib.P6 * comp_temp;
  partial_data2 = dev->calib.P7 * (comp_temp * comp_temp);
  partial_data3 = dev->calib.P8 * (comp_temp * comp_temp * comp_temp);
  partial_data4 = dev->calib.P5 + partial_data1 + partial_data2 + partial_data3;

  partial_data1 = dev->calib.P2 * comp_temp;
  partial_data2 = dev->calib.P3 * (comp_temp * comp_temp);
  partial_data3 = dev->calib.P4 * (comp_temp * comp_temp * comp_temp);
  out1 = (float)dev->calib.P1 + partial_data1 + partial_data2 + partial_data3;

  partial_data1 = dev->calib.P9 * (comp_temp * comp_temp);
  partial_data2 = dev->calib.P10 * (comp_temp * comp_temp * comp_temp);
  partial_data3 = (float)uncomp_press;
  partial_data4 = partial_data4 + (partial_data1 * partial_data3) + (partial_data2 * partial_data3 * partial_data3);

  out2 = partial_data4 + (out1 * partial_data3);
  return out2;
}

HAL_StatusTypeDef BMP390_Read(BMP390_t *dev)
{
  uint8_t raw_data[6] = {0};
  
  // Read pressure (3 bytes) and temperature (3 bytes)
  if (BMP390_SPI_Read(BMP390_REG_DATA_0, raw_data, 6) != HAL_OK)
  {
    return HAL_ERROR;
  }

  uint32_t uncomp_press = (uint32_t)((raw_data[2] << 16) | (raw_data[1] << 8) | raw_data[0]);
  uint32_t uncomp_temp = (uint32_t)((raw_data[5] << 16) | (raw_data[4] << 8) | raw_data[3]);

  if (uncomp_press == 0 || uncomp_temp == 0)
  {
    return HAL_ERROR;
  }

  float comp_temp = BMP390_Compensate_Temp(dev, uncomp_temp);
  // comp_temp here is the raw compensated term, actual temperature is comp_temp / 2^16 (roughly)
  dev->temperature = comp_temp; // actual compensated temperature
  dev->pressure = BMP390_Compensate_Press(dev, uncomp_press, comp_temp);

  // Calculate altitude in meters based on the standard atmosphere formula:
  dev->altitude = 44330.0f * (1.0f - powf(dev->pressure / 101325.0f, 0.1902949f));

  return HAL_OK;
}

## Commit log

2026-06-20 Updated PCB, repo structure, readme
    [29aabad2d4b64f8e8e30d17471c1a1ad.obj, 29aabad2d4b64f8e8e30d17471c1a1ad.step, BMP390L.step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]
2026-06-21 bom added
    [BOM.csv]
2026-06-24 BOM update
    [BOM.csv, Igniters.kicad_sch, Interfaces.kicad_sch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]
2026-06-24 update bom
    [BOM.csv]
2026-06-24 Convert BOM.csv to a standard CSV format
    [BOM.csv]
2026-06-24 Update BOM.csv header format
    [BOM.csv]
2026-06-24 Add BOM section with component details to README
    Added a Bill of Materials (BOM) section to the README with detailed component listings, including capacitors, resistors, inductors, diodes, integrated circuits, connectors, and miscellaneous items.
2026-06-24 Add schematics section with images to README
    Added schematic images section to README.
2026-06-24 added schematic photos
2026-06-24 Fix heading format for schematics section

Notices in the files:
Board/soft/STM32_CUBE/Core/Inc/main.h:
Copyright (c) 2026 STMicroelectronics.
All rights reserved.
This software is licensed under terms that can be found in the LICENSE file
